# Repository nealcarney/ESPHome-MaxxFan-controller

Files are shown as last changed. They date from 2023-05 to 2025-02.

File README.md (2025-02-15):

# MaxxFan and air conditioner controller

This project has two samples, both use an ESP32-based controller to control a MaxxFan using ESPHome and Home Assistant. The original solution also can control a Houghton air conditioner (or any AC using IR remote).
Preview

## MaxxFan Features

### MaxxFan only

- Control MaxxFan by emulating the wall-mount remote control which you connect via RJ-45.
- Toggle for power on/off, hood open/close, and direction intake/exhaust. Slider to control fan speed from 10% to 100%.

### MaxxFan and Houghton AC

- Temperature and humidity sensor.
- Overall power consumption measurement to facilitate monitoring. Also added board voltage measurement to facilitate trouble alerts.
- ‘Resynchronize’ feature in case HA gets out of sync with fan. If someone manually presses the MaxxFan control panel, HA won’t know about it and will be out of sync. Pressing the resync button will send an IR command to set the MaxxFan at a predetermined state; will also adjust UI and tracking logic in HA to same state.
- Keeps track of uptime, firmware status, and allows for reset.

## AC/heatpump features

- Controls the the AC/heatpump using IR transmitter to send commands to set heat/cool mode, fan speed, and power on/off. Temperature setting explained below.  The IR codes embedded in my ESPHome code is specific to Houghton AC, but you can substitute with appropriate codes for your particular AC unit.
- One of the downsides of most rooftop AC units is that the temperature sensor is located in the return air duct in the middle of the ceiling control panel. That is simply too close to the conditioned air output, especially since the air exiting the side and rear air vents immediately bounces off the wall and back toward the return air duct. So the built-in sensor gets inaccurate readings of actual room temperature, and the units tend to short-cycle. That definitely is the case with mine prior to this modification.
- So rather than use the built-in thermostat and let the unit determine on-off state, my controller takes over the temperature monitoring and on/off logic. It sends an ON command at max temp when the actual room temp is outside of desired temp band, and an OFF command once target temp is achieved. It only needs to use two temperatures: max low is 60F and max high is 85F.

## Known issues

The schematics and PCB are a prototype!!!  Please do not try to use as-is.  Later I will update with more info on what I had to modify to make v1.0 work, and what has changed with v1.1 which has not been tested.

## Links

- [PCB design files](https://oshwlab.com/ncarney/maxxfan-controller)
- [Youtube demo of functionality](https://youtu.be/xNdgwMG5jzs)
- [Post on Ford Transit USA Forum with more Home Assistant info](https://www.fordtransitusaforum.com/threads/home-assistant-for-van-automation.90215/post-1245570)
- [Post on Ford Transit USA Forum with more MaxxFan Houghton Controller discussion](https://www.fordtransitusaforum.com/threads/maxxfan-houghton-controller-for-home-assistant.94841/post-1245938)
- [AHT21 housing on Thingiverse](https://www.thingiverse.com/thing:5200358)

## Repository Structure

- `/homeassistant/` - Contains Home Assistant and ESPHome configuration files
  - `/esphome/` - ESPHome configuration and custom components
    - `maxxfan.yaml` - Full configuration with MaxxFan and AC control
    - `maxxfan-lite.yaml` - Simplified configuration for MaxxFan only
    - `custom_outputs.h` - Custom C++ code for MaxxFan control
  - `/www/` - Web assets for Lovelace UI customization
- `/MaxxFan-Controller-Lite/` - Contains the MaxxFan-Controller-Lite hardware files designed in Fusion 360
  - You can order the [MaxxFan only boards on PCBWay](https://www.pcbway.com/project/shareproject/W829927AS1Y4_WALTERS_schematic_v24_2025_01_10_53f183b7.html)
- And the PCB design files for the MaxxFan + Houghton AC are hosted separately on [OSH Lab](https://oshwlab.com/ncarney/maxxfan-controller)

## Notes

- The homeassistant folder contains a www folder.  This contains the dependencies needed for some of the Lovelace UI elements that I used.  If interested you can install in your own www folder and then add to the resources section of your dashboard management.

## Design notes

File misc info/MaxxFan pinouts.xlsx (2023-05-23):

MaxxFan | Action | Real | Color
2,3 | Fan on/off | 6,7 | Gr,BrWh
1,3 | Fan increase | 6,8 | Gr,Br
1,4 | Fan decrease | 5,8 | BlWh,Br
2,4 | Fan direction | 5,7 | BlWh,BrWh
2,5 | Fan auto | 4,7 | Bl,BrWh
1,3,4 | Fan open/close | 5,6,8 | BlWh,Gr,Br
Br=Ground
BrWh=Ground
1 | 8
2 | 7
3 | 6
4 | 5
5 | 4
6 | 3
7 | 2
8 | 1

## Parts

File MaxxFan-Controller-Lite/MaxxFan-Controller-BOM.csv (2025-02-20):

Qty | Value | Device | Package | Parts | Description | CREATED_BY | DATASHEET-URL | DIGIKEY_PARTNO | DIGI_KEY_PART_NUMBER | MANUFACTURER | MOUNT | MPN | PART-NUMBER | POPULARITY | TYPE | VALUE | XPXC
1 | 61300711121 | 61300711121 | 61300711121 | J2 | CONN HEADER VERT 7POS 2.54MM | PCBLayout.com |  |  | 732-5320-ND | Wurth Electronics Inc. |  | 61300711121
1 | 615008148521 | 615008148521 | 615008148521 | J1 | WR-MJ Modular Jack Horizontal Plastic 8P8C Tab Up |  | https://www.we-online.com/redexpert/spec/615008148521?ae |  |  |  | THT |  | 615008148521 |  | Horizontal | 615008148521 | 8P8C
5 | G6L-1PDC5 | G6L-1PDC5 | G6L-1PDC5 | R1, R2, R3, R4, R5 | RELAY TELECOM SPST 1A 5VDC | PCBLayout.com |  | Z1228-ND |  | Omron Electronics Inc-EMC Div |  | G6L-1P DC5
1 | ULN2003AN | ULN2003AN | DIL16 | IC1 | DRIVER ARRAY |  |  |  |  |  |  |  |  | 3

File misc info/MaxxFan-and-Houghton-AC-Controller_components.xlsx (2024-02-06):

ESPHome-MaxxFan-controller Component List
Name | Designator | Footprint | Quantity | Manufacturer Part | Manufacturer | Web link
TSAL6200 | IR1 | LED-TH_BD5.0-P2.54-FD | 1 | SFH-4546 | OSRAM | https://www.mouser.com/ProductDetail/ams-OSRAM/SFH-4546?qs=VcOkZLzzauarreCVxaCHEQ%3D%3D
TSAL6200 | IR2 | LED-TH_BD5.0-P2.54-FD | 1 | SFH-4544 | OSRAM | https://www.mouser.com/ProductDetail/ams-OSRAM/SFH-4544?qs=cd3lnLqJ6yVRMydznUbySw%3D%3D
ESP32 | A1 | D1-MINI-ESP32 | 1 | ESP32 |  | https://www.amazon.com/gp/product/B07BK435ZW
INA226 | A2 | INA226 MODULE | 1 | INA226 |  | https://www.amazon.com/gp/product/B0B799T8MX
MINI360BUCK | A3 | MINI360BUCK | 1 | Mini360 |  | https://www.amazon.com/gp/product/B07T7L51ZW
G6L-1P-DC5 | K1,K2,K3,K4 | RELAY-TH_G6L-1P-DCXX | 4 | G6L-1P-DC5 | OMRON | https://www.mouser.com/ProductDetail/Omron-Electronics/G6L-1P-DC5?qs=sQVrL4YZhsQ8oRG2i%2FXEVA%3D%3D
438600001 | RJ1 | RJ45-TH_438600001 | 1 | 438600001 | MOLEX | https://www.mouser.com/ProductDetail/Molex/43860-0001?qs=MuwpYaHj7506cO9je6gUDA%3D%3D
ULN2803 | U1 | DIP-18_L23.0-W6.5-P2.54-LS7.6-BL | 1 | ULN2803APG | TOSHIBA | https://www.amazon.com/gp/product/B08CX79JSQ

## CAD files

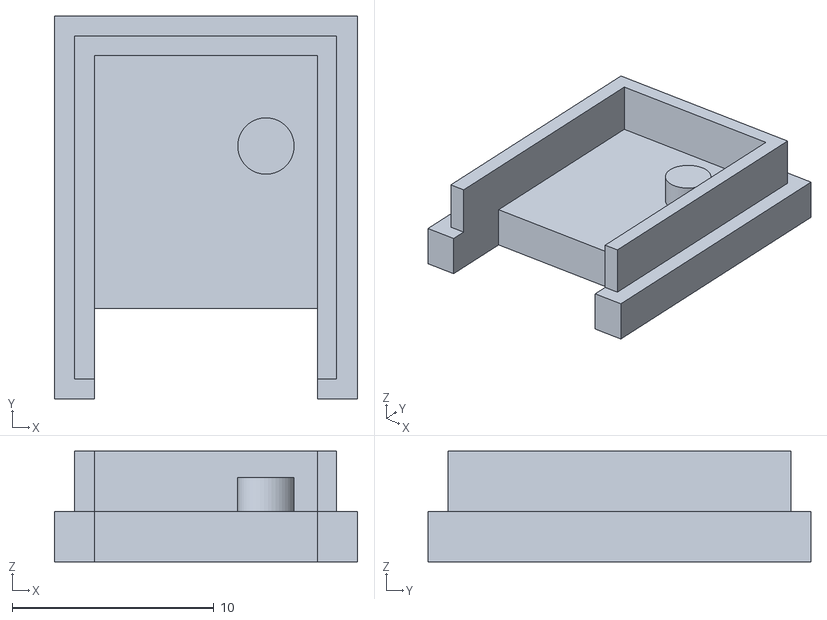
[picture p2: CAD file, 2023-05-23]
3D print AHT21/aht20housingback.stl
15.1 x 19.0 x 5.50

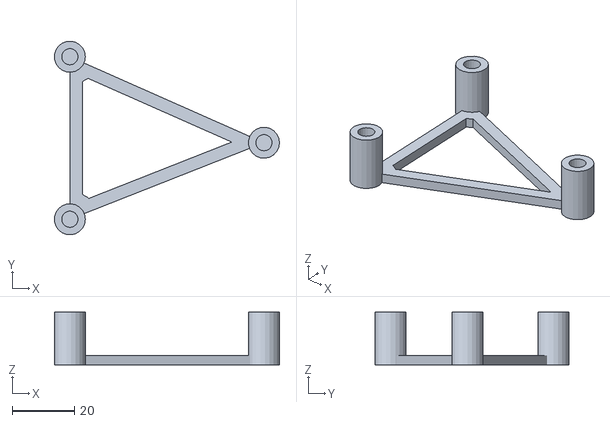
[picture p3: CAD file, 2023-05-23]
3D print support/MaxxFan board support v3.stl
72.4 x 62.3 x 17.0

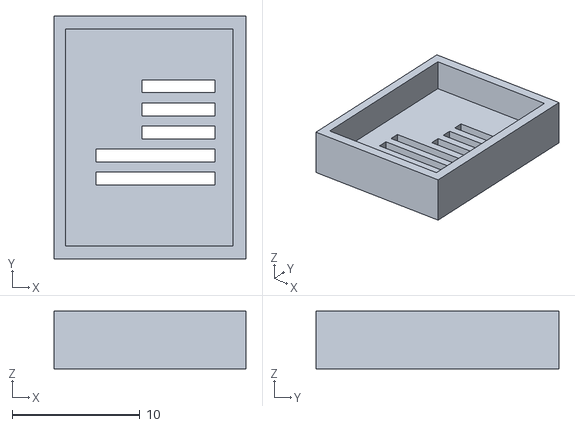
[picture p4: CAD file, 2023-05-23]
3D print AHT21/aht20housingfront.stl
15.0 x 19.0 x 4.50

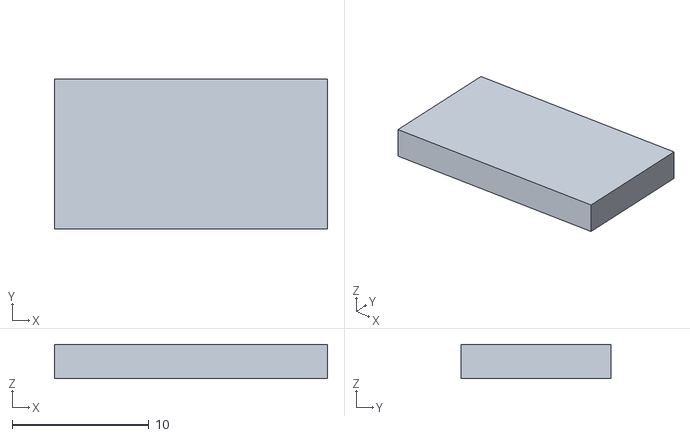
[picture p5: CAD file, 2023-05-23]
3D print support/INA226 support.stl
20.0 x 11.0 x 2.50

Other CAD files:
3D print support/INA226 support.skp
3D print support/MaxxFan board support v3.skp
MaxxFan-Controller-Lite/MaxxFan Controller v33.f3z

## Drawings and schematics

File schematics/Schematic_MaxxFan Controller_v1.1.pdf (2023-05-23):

+5V

## Power

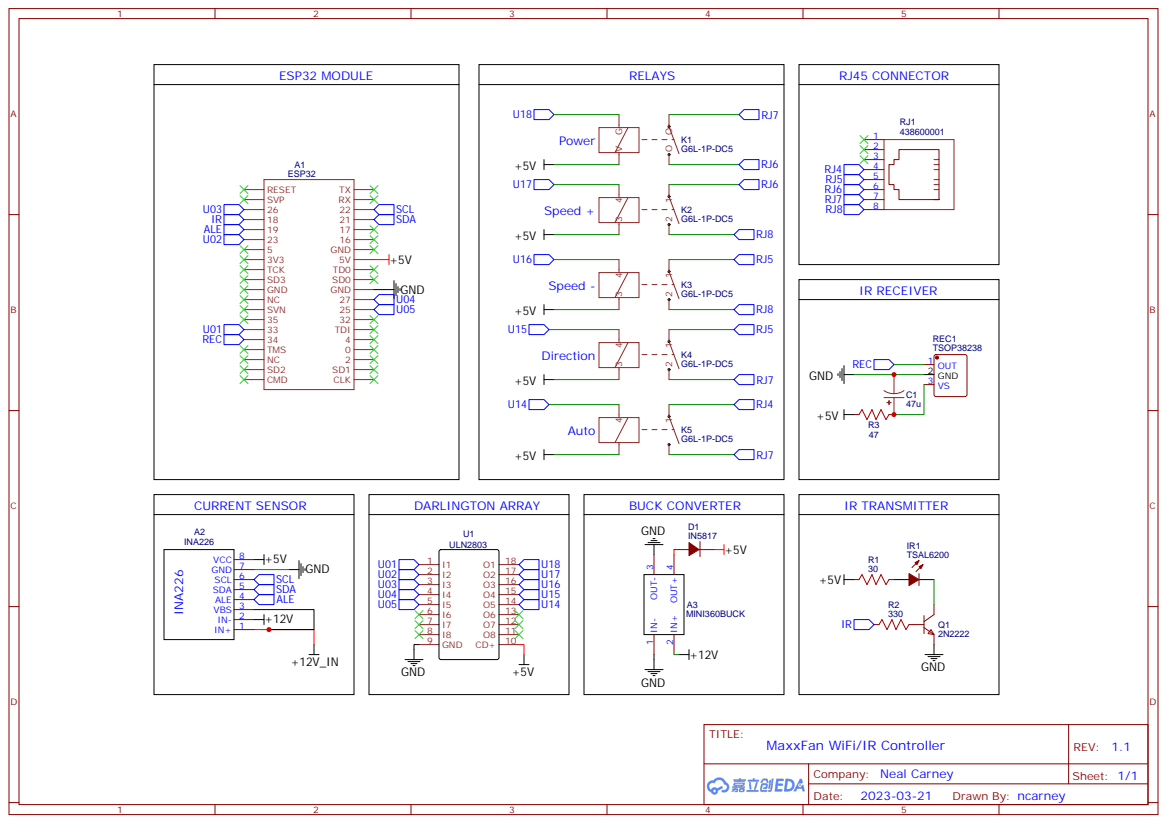
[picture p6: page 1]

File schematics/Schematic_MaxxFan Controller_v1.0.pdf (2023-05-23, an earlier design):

## Power

## Speed +

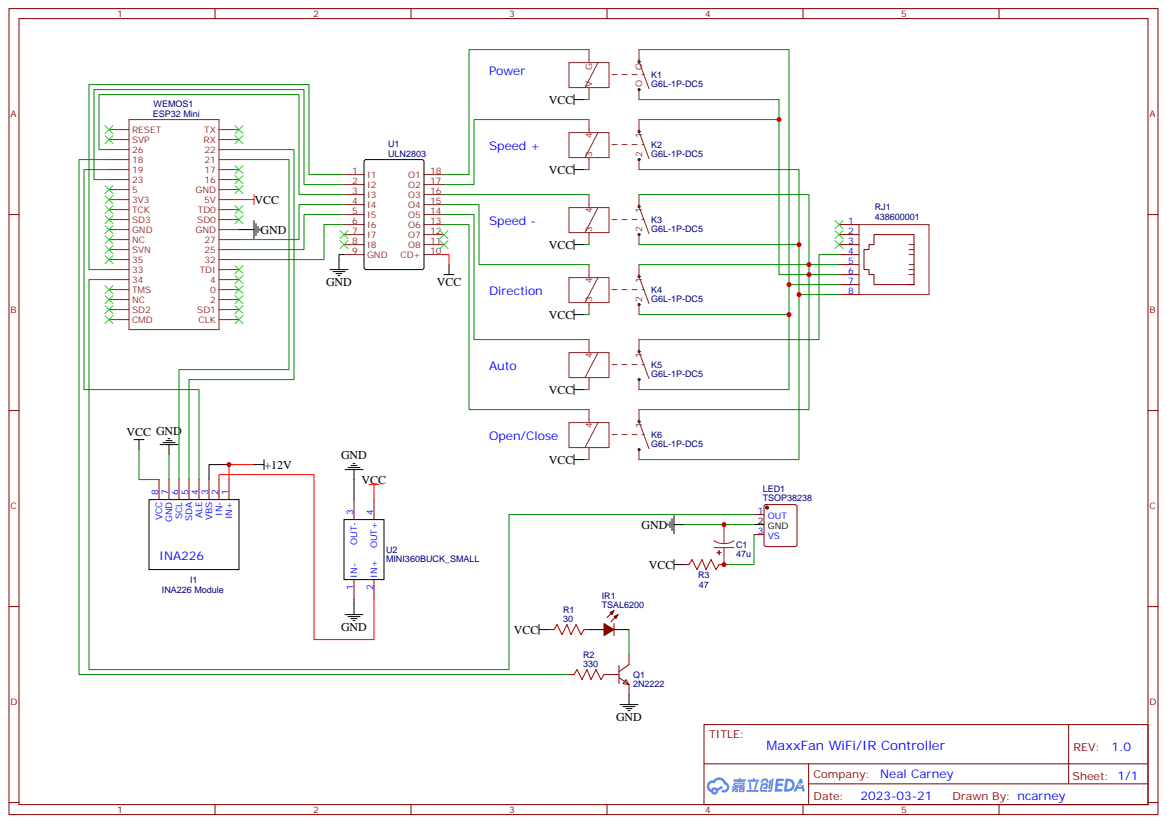
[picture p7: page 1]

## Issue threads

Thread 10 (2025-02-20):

FEATURE: Support mutiple MaxxFans from one ESP32

askpatrickw, 2025-02-20:
This just occured to me that we can use a single ESP32 to control more than one fan, it would just be different pin assignments for the different relays. Since I'm using Olimex ESP32 POEs, this would save me a POE port (and a tiny bit of power).

I'm not sure what all would need to be refactored yet, but I will sort this out and make a PR.

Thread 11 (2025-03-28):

Custom Components are deprecated

askpatrickw, 2025-03-28:
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

https://esphome.io/guides/contributing#a-note-about-custom-components

I'll work out a plan ...

nealcarney, 2025-03-29:
Bummer.  Thanks for looking into this.  I sold my original van so I no longer have an operative board.  I only retained the spare v1 PCBs.

nealcarney, 2025-03-30:
Check out https://github.com/robertklep/esphome-custom-component

nealcarney, 2025-04-07:
Thanks for the developing the fix Patrick!

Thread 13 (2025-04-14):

custom components

Darkside2016, 2025-04-14:
INFO ESPHome 2025.3.3
INFO Reading configuration /config/esphome/maxxfan.yaml...
Failed config

output.custom: [source /config/esphome/maxxfan.yaml:170]

  The "custom" component has been removed. Consider conversion to an external component.
  https://esphome.io/guides/contributing#a-note-about-custom-components.
  platform: custom
  type: binary
  lambda: |-
    auto my_power_output = new PowerOutput();
    App.register_component(my_power_output);
    return {my_power_output};
  outputs:
    id: output_power

nealcarney, 2025-04-14:
Are you using maxxfan.yaml or maxxfan-lite.yaml?  This was fixed last week in maxxfan-lite.yaml and the associated new files that were implemented.  Check out this commit:  https://github.com/nealcarney/ESPHome-MaxxFan-controller/pull/12/commits/7c8ab4c64fc95eaa3c6454beffb3aa1e3384c228.  I think you can easily update the maxxfan.yaml file with the same changes that were made to maxxfan-lite.yaml.  Unfortunately, I no longer have the original controller board so I am not actively maintaining the original version.

nealcarney, 2025-04-14:
Yes, that was one of the possible solutions I identified; glad that you tried it.  Let me know how it goes once you flash it.

Darkside2016, 2025-04-14:
I see here on Git that you have a PCB with 6 relays.
But if I follow the link for the PCB design, there are only 4 relays.

Is there a chance to get the PCB layout with the 6 relays?

nealcarney, 2025-04-15:
If you use EasyEDA, I think you should be able to see prior versions of the board.with 5 and 6 relays; you just need to use the "switch version" function when right clicking on the project.

HOWEVER...

- v1.0 of the board has six relays but definitely doesn't work.  You only need five relays to control the fan since the lid open/close function is done by simultaneous closure of two of the other relays.  I had to manually fix some of the traces on the board to fix this issue.
- v1.1 of the board has five relays.  One of those relays controls the "auto" function of the fan, which really isn't necessary since you will likely be controlling the fan using a thermostat connected to your ESP32.  v1.1 was never produced or tested.
- v1.2 of the board has four relays, which is all you really need (speed up, speed down, power, direction), but no relay for the auto function.  v1.2 was also never produced or tested.

Honestly, unless you need/want the extra functions of my board (power monitoring and IR stuff), I recommend that you go with the maxxfan-lite version recently developed by @askpatrickw.  His board will provide the basic Maxxfan controls and will be easier to implement.  If you want to go with the full version with IR and power monitoring, you need to read [this post](https://www.fordtransitusaforum.com/threads/home-assistant-for-van-automation.90215/page-17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) .  Beside v1.2 never being tested, I think the other thing that might be difficult, depending on your skills, is that the resistor on the INA226 board needs to be desoldered and replaced in order for the power monitoring to work (aside from remainder of the soldering work).  The board developed by @askpatrickw can be ordered with all the components installed and ready to go.

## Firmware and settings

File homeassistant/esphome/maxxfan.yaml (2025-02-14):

esphome:
  name: maxxfan
  friendly_name: MaxxFan
  includes:
    - custom_outputs.h
  on_boot:
    # Lowest priority; wait until everything else is done
    priority: -100
  # Need to set initial values during boot sequence
  # Two situations:   1: ESP32 was restarted without disconnecting MaxxFan power
  #                   2: Both ESP32 and MaxxFan were re-powered
  # 1. For ESP32 restart, need to use restore values saved to flash by ESP32
  # 2. For full re-power, the MaxxFan default values are:
  #    power = off; speed = 4; direction = exhaust (reverse); cover = closed
    then:
      lambda: |-
        ESP_LOGD("boot", "Executing on_boot logic");
        if (!id(is_restart)) {
          // Not a restart condition, therefore likely a full re-power.
          // Apply default MaxxFan settings otherwise it will just 
          // use settings which should have been saved by ESP32.
          ESP_LOGD("boot", "Setting globals to re-power values");
          id(actual_fan_power) = 0;     //Off
          id(actual_fan_speed) = 4;     //40%
          id(actual_fan_direction) = 1; //Exhaust
          id(actual_fan_cover) = 0;     //Closed
        }
        ESP_LOGD("boot", "Updating entities with values from globals");
        // Usually you can set power and speed in same call, but when you do it
        // sets power first, which will immediately turn on with speed of 10
        // which is the default setting when speed is 0/unknown. So make two calls
        // and set the speed first.
        auto call = id(MaxxFan).make_call();
        call.set_speed(id(actual_fan_speed));
        call.perform();
        call.set_state(id(actual_fan_power));
        call.perform();
        id(maxxfan_direction).publish_state(id(actual_fan_direction));
        id(maxxfan_cover).publish_state(id(actual_fan_cover));
        ESP_LOGD("boot", "Power set to: %d", id(actual_fan_power));
        ESP_LOGD("boot", "Speed set to: %d", id(actual_fan_speed));
        ESP_LOGD("boot", "Direction set to: %d", id(actual_fan_direction));
        ESP_LOGD("boot", "Cover set to: %d", id(actual_fan_cover));
        // Set thermostat fan speed to AUTO if UNKNOWN
        if (id(houghton).fan_mode == NULL) {
          auto call = id(houghton).make_call();
          call.set_fan_mode("AUTO");
          call.perform();
        }
        // Reset flags for next boot
        id(is_restart) = false;
        id(is_boot_finished) = true;
  on_shutdown:
  # Clicking Restart button in UI will trigger controlled shutdown/restart vs. just 
  # disconnecting powerfrom both the fan and ESP32, which will not trigger on_shutdown.
    priority: 600
    # Set indicator
    then:
      - lambda: |-
          id(is_restart) = true;
          ESP_LOGD("shutdown", "Restart set to: %d", id(is_restart));

esp32:
  board: wemos_d1_mini32

# Enable logging
logger:

# Enable Home Assistant API
api:
  encryption:
    key: "TcGiPF//EV3XtI5uFQUfC2PY3SC0JvdREHwTnCp1Aug="

ota:
  password: "1ac996384f7272b220c931ca7cebaab5"

wifi:
  ssid: !secret wifi_ssid
  password: !secret wifi_password

  # Enable fallback hotspot (captive portal) in case wifi connection fails
  ap:
    ssid: "Maxxfan Fallback Hotspot"
    password: "0nXMOS1Bnf0P"

captive_portal:

i2c:
  # Standard i2c pins for ESP32
  sda: 21
  scl: 22
  scan: true
  id: bus_a

globals:
  # Need this to know if on_boot is a restart or repower
  - id: is_restart
    type: bool
    initial_value: '0'
    restore_value: true
  # Need this to know if boot finished; don't execute output actions
  # unless boot has finished to prevent UI overriding actual values
  - id: is_boot_finished
    type: bool
    initial_value: '0'
    restore_value: false
  # Used to keep track of actual settings in fan itself.  UI controls 
  # need to be synchronized to match these actual settings. Required 
  # because speed adjustment requires incremental button presses, and 
  # MaxxFan automatically changes cover state whenever power is pressed.
  - id: actual_fan_speed
    type: int
    initial_value: '4'
    restore_value: true
  - id: actual_fan_power
    type: bool
    initial_value: '0'
    restore_value: true
  - id: actual_fan_direction
    type: bool
    initial_value: '1'
    restore_value: true
  - id: actual_fan_cover
    type: bool
    initial_value: '0'
    restore_value: true
  # GPIO pin configurations
  - id: gpio_down_pin
    type: int
    initial_value: "26"
    restore_value: no
  - id: gpio_up_pin
    type: int
    initial_value: "23"
    restore_value: no
  - id: gpio_power_pin
    type: int
    initial_value: "33"
    restore_value: no
  - id: gpio_direction_pin
    type: int
    initial_value: "27"
    restore_value: no
  - id: gpio_auto_pin
    type: int
    initial_value: "25"
    restore_value: no
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

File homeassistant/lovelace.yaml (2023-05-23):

title: Van
views:
  - theme: Backend-selected
    path: default_view
    title: Van
    icon: mdi:van-utility
    badges: []
    cards:
      - type: conditional
        conditions:
          - entity: binary_sensor.maxxfan_status
            state: 'off'
          - entity: binary_sensor.maxxfan_status
            state_not: 'on'
        card:
          type: entities
          entities:
            - entity: binary_sensor.maxxfan_status
              icon: mdi:wifi-off
              secondary_info: last-changed
              name: Disconnect time
          title: MaxxFan
      - type: conditional
        conditions:
          - entity: binary_sensor.maxxfan_status
            state: 'off'
          - entity: binary_sensor.maxxfan_status
            state_not: 'on'
        card:
          type: entities
          entities:
            - entity: binary_sensor.maxxfan_status
              icon: mdi:wifi-off
              secondary_info: last-changed
              name: Disconnect time
          title: Air conditioner
      - type: conditional
        conditions:
          - entity: binary_sensor.maxxfan_status
            state: 'on'
          - entity: binary_sensor.maxxfan_status
            state_not: 'off'
        card:
          type: entities
          show_header_toggle: false
          state_color: false
          title: MaxxFan
          entities:
            - card_type: horizontal-stack
              cards:
                - entity: switch.maxxfan_direction
                  name: Direction
                  template: maxxfan_buttons
                  type: custom:button-card
                  style: |
                    ha-card {
                      {% if is_state('fan.maxxfan_fan','off') %}
                        color: var(--disabled-text-color);
                        pointer-events: none;
                      {% endif %}
                    }
                  state:
                    - icon: mdi:rotate-left
                      name: Exhaust
                      value: 'on'
                    - icon: mdi:rotate-right
                      name: Intake
                      value: 'off'
                - entity: switch.maxxfan_cover
                  name: Cover
                  template: maxxfan_buttons
                  type: custom:button-card
                  state:
                    - icon: mdi:arrow-up
                      name: Open
                      value: 'on'
                    - icon: mdi:arrow-down
                      name: Closed
                      value: 'off'
                - entity: fan.maxxfan_fan
                  name: Power
                  template: maxxfan_buttons
                  type: custom:button-card
                  state:
                    - icon: mdi:fan
                      name: 'On'
                      value: 'on'
                    - icon: mdi:fan-off
                      name: 'Off'
                      value: 'off'
              type: custom:hui-element
            - type: custom:slider-entity-row
              entity: fan.maxxfan_fan
              min: 0
              max: 100
              step: 10
              hide_when_off: false
              name: Speed
              icon: none
              full_row: true
            - entity: sensor.maxxfan_temperature
              type: custom:multiple-entity-row
              state_header: Temperature
              name: Climate
              format: precision0
              entities:
                - entity: sensor.maxxfan_humidity
                  name: Humidity
                  styles:
                    width: 75px
                    text-align: center
            - entity: sensor.maxxfan_power
              type: custom:multiple-entity-row
              state_header: Power
              name: Electric
              secondary_info:
                entity: sensor.maxxfan_board_voltage
                name: 'ESP32:'
              entities:
                - entity: sensor.maxxfan_voltage
                  name: Voltage
                  styles:
                    width: 50px
                    text-align: center
                - entity: sensor.maxxfan_current
                  name: Current
                  styles:
                    width: 50px
                    text-align: center
            - entity: button.maxxfan_ir_synchronize
              name: Re-synchronize
              icon: mdi:remote
            - card_type: horizontal-stack
              cards:
                - type: custom:button-card
                  label: |
                    [[[
                      return "Uptime: " + states['sensor.uptime'].state
                    ]]]
                  name: |
                    [[[
                      var installed = states['update.maxxfan_firmware'].attributes.installed_version;
                      var latest = states['update.maxxfan_firmware'].attributes.latest_version;
                      if (installed == latest)
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

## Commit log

2025-02-12 Abbreviated yaml for relay only control
2025-02-14 Move pin configuration to YAML file
2025-02-14 Add MaxxFan Lite design files and update README
    [MaxxFan Controller v33.f3z]
2025-02-14 Update README.md
    add PCBWay link
2025-02-19 Add BOM
    Adds Build of Materials, the components to put on the PCB.
    [MaxxFan-Controller-BOM.csv]
